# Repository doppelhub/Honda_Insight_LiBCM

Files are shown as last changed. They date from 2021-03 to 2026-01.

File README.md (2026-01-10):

# Honda_Insight_LiBCM
Replacement BCM for G1 Honda Insight Lithium Conversion
Licensed under Creative Commons - Attribution - ShareAlike 3.0
Project created and maintained by insightcentral.net user 'mudder' (a.k.a. John Sullivan).

LiBCM is a replacement computer that allows the G1 Honda Insight (2000-2006) to safely use modern lithium traction batteries.

LiBCM replaces the OEM Battery Control Module (BCM).  LiBCM is presently offered as two different 'Kits':
-'5AhG3 LiBCM Kit' uses 12S & 18S lithium battery modules from various modern Honda hybrids, or;
-'47Ah LiBCM Kit' uses 12S Samsung SDI lithium battery modules

While other lithium battery types are theoretically supported, integrating them with LiBCM is beyond the design goals for this project.  A few customers are using non-supported modules, but it requires custom BMS harnesses and also cell discharge curve characterization to create a Voc->SoC lookup table.

LiBCM officially supports the following lithium configurations:
-'5AhG3' - 48S ONLY, or;
-'47Ah'- either 48S or 60S.

NO OTHER CONFIGURATION is officially supported.  While the PCB's onboard BMS supports anywhere from 6S to 60S, you're on your own (firmware-wise) if you want to run anything besides 48S.  Future firmware updates might allow 54S and/or 60S support. 

See linsight.org for more information.

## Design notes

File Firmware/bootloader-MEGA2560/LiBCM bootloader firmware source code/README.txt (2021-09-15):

This custom MEGA2560 bootloader allows LiBCM to initially power up fast enough to not cause P1648 CEL.

A standard MEGA2560 will otherwise work with LiBCM, but will cause P1648 at the first key-on event after the IMA power switch is turned on.  After that, as long as LiBCM has not turned itself off (e.g. due to low battery), LiBCM will remain powered up, hence no P1648 error.

If you purchased an LiBCM PCB from me, then it already has the LiBCM bootloader on it.
If you're programming your own MEGA2560, then you can load the .hex file onto your MEGA using the "Arduino as SPI burn bootloader" method (do a google search).

To compile the file (e.g. if you don't want to use the pre-compiled hex file), you will need to install avr-gcc (e.g. via homebrew in MacOS), and then make the file ("make mega2560").  This is an advanced method, and if you don't know how to do it, just install the hex file instead.

The contents of this folder generate the "stk500boot_v2_mega2560.hex" file, which is then uploaded to the Arduino MEGA.

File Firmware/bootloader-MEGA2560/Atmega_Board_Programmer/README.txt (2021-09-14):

This tool is used to create an ISP that will program an Arduino Uno to program the LiBCM bootloader onto an Arduino Mega.  This custom bootloader is identical to the shipping version, except that on power-up it checks to see if the key is turned on, in which case the bootloader immediately jumps to LiBCM firmware.

See instructions here:
http://www.gammon.com.au/bootloader

Load Atmega_Board_Programmer.ino onto an Arduino Uno, then connect it to the mega as shown in the above link.  

Open debug window at 115200 and follow instructions

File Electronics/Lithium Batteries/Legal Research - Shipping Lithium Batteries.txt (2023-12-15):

Summary:
For modules up to 300 Wh, you can ship USPS ground with:
-Limited Quantity label, and
-"Lithium batteries - forbidden for transport aboard aircraft and vessel"

No additional paperwork is required (these medium-sized cells are exempted by 49CFR173.185(c):
https://www.ecfr.gov/current/title-49/subtitle-B/chapter-I/subchapter-C/part-173/subpart-E/section-173.185
"[cells under 300 Wh] are exempt from the requirements in subparts C through H of 49CFR172

Therefore, since modules over 300 Wh are NOT exempt, the must include the following additional markings:
-UN3480 (requires hazardous shipping license at UPS... but maybe not USPS?)
-Class 9 Lithium Battery label

//////////////////////////////////////////

https://pe.usps.com/text/pub52/pub52c3_003.htm#ep898369

Postal Service standards generally limit the mailing of hazardous materials to Limited Quantity surface materials or Limited Quantity air materials as defined in 332 through 336, that meet USPS quantity limitations and packaging requirements. This allowance is limited to the following:
...
Lithium batteries, dry ice, and magnetized materials, as permitted in 349.

...

332 Limited Quantity:
https://pe.usps.com/text/pub52/pub52c3_011.htm
"A limited quantity of a hazardous material is the maximum amount of a specific hazardous material exempted from DOT labeling or packaging requirements in 49 CFR. To be eligible to ship under the DOT Limited Quantity provision, a hazardous material must list an exception in column 8A of the Hazardous Materials Table in 49 CFR 172.101"

49CFR172.101 column 8A for "lithium ion batteries" states:
-must adhere to 49CFR173.185 packaging requirements
-173.27 & 175.75 non-passenger aircraft package weight limit: 35 kg

///////////////////////////////////

349 (https://pe.usps.com/text/pub52/pub52c3_027.htm#ep900056)

349.2 Mailability
... lithium batteries ... are permitted within the specified limits provided in ... 349.222, 349.23, and 349.24

///////////////////////////////////

349.222 (same link as above)
In summary: Lithium batteries with cells weighing up to 5 pounds are mailable via surface transportation.

349.4(b)
For surface transportation, parcels containing mailable Class 9 materials must be plainly and durably marked on the address side with an approved DOT Limited Quantity ground marking unless specified in 221.1 and 325.1 (see 325.4). Surface shipments bearing the Limited Quantity ground marking are not required to include the proper shipping name and identification number.

/////////////////////////////////////
/////////////////////////////////////

UPS Dangerous Goods contract
UPS Hazardous Materials Contract Service
In order to ship hazardous materials/dangerous goods with UPS, you must enter into an Agreement that ensures compliance with applicable Regulations as well as UPS carrier requirements.  In order to use this service, you must:
-Have a UPS.com user name
-Have a shipping account
-Be in compliance with all regulatory requirements and UPS's carrier variations

/////////////////////////////////////
UPS guidelines:
https://www.ups.com/assets/resources/webcontent/en_US/pack_ship_batteries.pdf

UPS does not allow UN3480 (Lithium Ion Batteries (by themselves)) without a "UPS Dangerous Goods Contract".
but does allow UN3481 (Lithium Ion Batteries contained in equipment)

"air shipments of lithium ion (UN3480) and lithium metal (UN3090) batteries without equipment must be sent as fully regulated dangerous goods when shipped with UPS, which requires a UPS Dangerous Goods contract."

"lithium ion or metal batteries may be classed as “packed with equipment” or “contained in equipment” when
the batteries accompany or are installed in apparatus for which the lithium batteries will provide electrical power for operation."

"For fully regulated shipments, the Class 9 Lithium Battery label is required."

"For ground shipments, the markings shown above are common in most countries around the world (see ADR SP 188, TDGR SP 34, or check local regulations). The U.S. additionally requires ground shipments of small lithium batteries to be identified as forbidden on passenger aircraft. The Cargo Aircraft Only label may be used, or either of the following statements, in letters at least 6 mm high:
-LITHIUM ION BATTERIES-
FORBIDDEN FOR TRANSPORT ABOARD PASSENGER AIRCRAFT"
^^^FedEx has the same requirement...
^^^...because this is a federal law: 49CFR173.185(C)(1)(iv):
"For transportation by highway or rail only, the lithium content of the cell and battery may be increased to ... 60 Wh for a lithium ion cell or 300 Wh for a lithium ion battery, provided the outer package is marked: “LITHIUM BATTERIES - FORBIDDEN FOR TRANSPORT ABOARD AIRCRAFT AND VESSEL.”"

"The U.S. also allows unique exceptions on the ground for medium lithium batteries, not recognized in other international regulations. For lithium ion, medium cells have > 20 Wh but ≤ 60 Wh; and medium batteries have > 100 Wh but ≤ 300 Wh.  Medium lithium cells/batteries may be shipped by ground as lightly regulated, provided they have the appropriate lithium ion or lithium metal mark (as shown above) and display the following marking:
LITHIUM BATTERIES—FORBIDDEN FOR TRANSPORT ABOARD AIRCRAFT AND VESSEL.”

Figure 8 - Flowchart (page 9):
Is lithium battery greater than 100 Wh? Yes
Is lithium battery less than 300 Wh OR cells less than 60 Wh? Yes
Does the package contain lithium ion batteries packed with equipment? NO
Does the package contain lithium ion batteries contained in equipment? NO
Is the gross package weight greater than 30 kg? NO
Result:
Your package does not need to be shipped as fully regulated Dangerous Goods. Please see U.S. DOT Hazardous Materials Regulations for further details about shipping requirements.
Required: Warning markings stating “Lithium Batteries – Forbidden for Transport Aboard Aircraft and Vessel,” lithium ion battery mark.

/////////////////////////////////////////////////////////////

https://www.ups.com/media/en/lithium_batteries_guidance.pdf

/////////////////////////////////////////////////////////////
Lots of packaging-specific examples:
https://www.rrc-ps.com/fileadmin/Dokumente/Shipment/Shipping_Guidelines_Lithium_Ion_Batteries_EN.pdf
5.2. Shipment of Lithium Ion Batteries > 100 Wh by Truck / Rail (ADR/RID), Sea Freight (IMDG)
A passed transportation test according section 38.3 of the UN Manual of Tests and Criteria is required!

Critical: Passing of safety tests for lithium batteries and cells (Refer to the UN Manual of Tests and Criteria
- UN/DOT 38.3). This will be indicated in the test summary document requested from your supplier.
• There are recordkeeping requirements for this testing which can be found in 49CFR173.185.

49CFR173.185:
https://www.ecfr.gov/current/title-49/subtitle-B/chapter-I/subchapter-C/part-173/subpart-E/section-173.185
"Beginning January 1, 2022 each manufacturer and subsequent distributor of lithium cells or batteries manufactured on or after January 1, 2008, must make available a test summary."

/////////////////////////////////////////////////////////////

Fedex course:
http://www.shipsafeshipsmart.com/ProductSubCats.aspx?SubCatID=5
https://www.fedex.com/content/dam/fedex/us-united-states/services/Shipping-Lithium-Batteries-via-FedEx-Ground.pdf

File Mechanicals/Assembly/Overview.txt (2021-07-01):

THIS IS A WORK IN PROGRESS

Assembly instructions:

0: Tear pack down to core.
	Keep:
	-Fan shroud (drill 0.75" hole)
	-QTY6 self-tapping screws
	-Side cover and QTY6 screws
	-QTY4 MCM bolts
	-QTY2 longest bolts
	-QTY2 high current spacers
	-QTY6 junction board bolts
	-QTY8 fan shroud bolts
	-Junction board (we'll modify below)
	-MCM'E' connector (we'll modify below)
	-Temp Sensor Harness (broken down as shown)
	-Core (with inserts) (we'll modify below)

1: Core modifications
	-Drill QTY3 0.75" holes for high current lead
	-Drill QTY6 holes for PCB
	-Add stickers

2: Batteries
	-Add stickers

2: Junction board modifications
	-Covers: 5

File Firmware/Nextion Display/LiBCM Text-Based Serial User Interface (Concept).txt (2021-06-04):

Welcome to LiBCM
version:1.21 2021APR17

'H' to Return to this Home screen
'P' to Return to Previous Screen

Enter command:
1: System Status
	Power-On Time: 1234 seconds
	Pack Configuration: 42S
		
	A: Display values since last reset
		Data Since Last Reset ('R' to reset):
		Vcell(min):	2456 mV @ C34
		Vcell(max):	3958 mV @ C34
		Vdelta:		0123 mV (C24-C32)
		Vpack:		123 Vmin, 145 Vmax
		SoC:		010% min, 078% max	
		Tpack:		10 C min, 45 C max
		Iregen(max):	078 A (actual) 
		Iassist(max):	134 A (actual)
		Total Assist:	1234 Ah (actual)
		Total Regen:	1456 Ah (actual)
		Time:		345232 s
	B: Display values since last full charge	
		Same as above, except 'Data Since Last Full Charge'
	C: Display realtime data
		U: Update Once
		C: Update Continuously ('Q' to stop)
		Vcell(min):	2456 mV @ C34
		Vcell(max):	3958 mV @ C34
		Vdelta:		0123 mV (C24-C32)
		Vpack:		123 V
		SoC:		010%	
		Tpack (min):	10 C
		Tpack (max):	12 C
		Ibatt:		078 A
		Key is: ON
		Grid Charger AC Present?: YES
		Grid Charger Powered: NO
		Grid Charger Power Output: 100%

	D: Read Raw Cell Voltages (mV)
		C: Update Continuously ('Q' to stop)
		C01-C12: 3245 3245 3245 3245 -  3245 3245 3245 3245 -  3245 3245 3245 3245
		C13-C24: 3245 3245 3245 3245 -  3245 3245 3245 3245 -  3245 3245 3245 3245
		C25-C36: 3245 3245 3245 3245 -  3245 3245 3245 3245 -  3245 3245 3245 3245
		C37-C48: 3245 3245 3245 3245 -  3245 3245 3245 3245 -  3245 3245 3245 3245
		C49-C60: 3245 3245 3245 3245 -  3245 3245 3245 3245 -  3245 3245 3245 3245
		C61-C72: 3245 3245 3245 3245 -  3245 3245 3245 3245 -  3245 3245 3245 3245
		C72-C84: 3245 3245 3245 3245 -  3245 3245 3245 3245 -  3245 3245 3245 3245
	
	E: Read Raw temperature data (degC)
		C: Update Continuously ('Q' to stop)
		GRN(Bay1): 34 C
		WHT(Inlet): 23 C
		YEL(Outlet): 35 C
		RED(Bay3): 29 C
		BMS_C01-C12: 30 C
		BMS_C13-C24: 30 C
		BMS_C25-C36: 30 C
		BMS_C37-C48: 30 C
		BMS_C49-C60: N/A
		BMS_C61-C72: N/A
		BMS_C72-C84: N/A

	F: Read Raw BATTSCI Data (from MCM)
		U: Update Once
		C: Update Continuously ('Q' to stop)

	G: Read Cell Balance Status
		Note: '1' if cell is balancing 
		C: Update Continuously ('Q' to stop)
		C01-C12: .... ..1. 1...
		C13-C24: .... .... ....
		C25-C36: .1.. .... ....
		C37-C48: .... .... ....
		C49-C60: .... 1... ....
		C61-C72: .... .... ....
		C72-C84: .... .... 1...

2: Configure Parameters
Note: These parameters cannot be change if a DIP switch on the PCB is set
	A: BMS Settings
		A: Minimum cell discharge voltage: 2750 mV
			Enter new cell Vmin ('P' to abort): 
			Example: '2750' sets Vmin to 2750 mV
			Set Vmin to 2750 mV? (Y/N)
		B: Maximum cell charge voltage: 4100 mV
			Enter new cell Vmax ('P' to abort): 
			Example: '4100' sets Vmax to 4100 mV
			Set Vmax to 4100 mV? (Y/N)
		C: Pack Ampacity: 4657 mAh
			Enter new pack size in mAh ('P' to abort):
			Example: '8000' sets pack size to 8000 mAh
			Set pack size to 8000 mAh? (Y/N)
		D: Pack SoC: 45.5%
			Enter new SoC percent as Integer ('P' to abort):
			Example: '76' sets SoC to 76%
			Note: This is the usable pack SoC, based on min/max cell voltage settings
			Set SoC to 76%? (Y/N)

	B: Temperature Settings
		A: Fans turn on at:	        23 C 
		B: Fans full speed at:	        35 C
		C: Fans disabled below:	        25% SoC
		D: Disable Grid Charging above: 45 C@pack

		N: OEM Sensor Names
			A: GRN: "Bay1"
				Enter new name for GRN temp sensor:
			B: WHT: "Inlet"
				Enter new name for WHT temp sensor:
			C: YEL: "Outlet"
				Enter new name for YEL temp sensor:
			D: RED: "Bay3"
				Enter new name for RED temp sensor:
		
	C: Grid charger settings
		E: Grid Charger installed?: Y
			Is grid charger installed? (Y/N): Y
		M: Disable Grid Charge Above SoC: 75%
			Enter new maximum grid charge SoC as Integer:
			Example: '70' disables grid charger above 70% SoC 

	D: MCM Voltage/Current Spoofing
		P: Presets
			Configure Voltage/Current Hacks (existing: B)
			A: 42S with no Current Hack
			B: 48S with no Current Hack
			C: 42S with +40% Current Hack
			D: 48S with +40% Current Hack
			
		A: Scale Current sent to MCM by: 100%
			Enter new scaled current percentage as Integer ('P' to abort):
			Note: This is the actual multiplier applied to the raw current sensor reading.
			Note: Any value besides '100%' requires external hardware modifications to MCM.
			Example: '+40% current hack' is 72% (1/1.4), because 140A*0.71=100A 

		B: Scale Voltage sent to MCM @ 0% SoC by: 100%
			Note: This value must be between 80-100%
		C: Scale Voltage sent to MCM @ 100% SoC by: 80% 
			Note: This value must be between 80-100%
			Note: Useful for high voltage packs
		Note: VPIN must be connected to LiBCM for this to work.

	F: Restore Defaults
		Restore LiBCM to default values.  This cannot be undone.
		RESET ALL STORED DATA? (y/n):

	G: Debug
		A: Configure METSCI FRAME 'A'
		B: Configure METSCI FRAME 'B'
		C: Configure METSCI FRAME 'C'
		D: Configure METSCI FRAME 'D'
		E: Toggle Fans
		F: Toggle Grid Charger
		G: Set Grid Charger PWM
		J: Restart

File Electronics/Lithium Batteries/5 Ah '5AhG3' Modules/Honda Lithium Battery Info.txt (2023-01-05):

Honda Models
STEP WGN SPADA
SPORT HYBRID i-MMD
FREED i-DCD
NSX
i-MMD

CR-Z (EH5)(2011-2014):
	IMA PN: 1D010-RBJ-C00 or 1D010-RBJ-A00

Accord Hybrid (EH5)(2014-2015):
	IMA PN: 1D070-5K1-406RM & 1D070-5K1-405RM & 5 more
	Found eBay picture with blue cells shown.

Accord Hybrid (EHW5)(2018-2020):
	IMA PN: 1D070-6C2-305
	Found eBay picture showing assembled battery at 259 V
	It's probably this car... maybe new insight.

Clarity Fuel Cell (EHW5)(2017-2020):
	IMA PN: 1D100-5WM-A01RM

NSX (EHW5)(2016)

Honda Insight (2019):
	IMA PN: 1D070-6L2-A00
	Found eBay picture showing assembled battery

Battery info:
Make: Blue Energy (Panasonic?)
Model: EHW5
Ah: 5 (charged to 4.2 volts)
Vnom: 3.6
Operating range: -30 degC to 55 degC (131 degF)
Cycle life: 50,000 (@10-85% SoC), continuous 40A charge/discharge!
Time Life: 10 years
Recommended charge/assist current: 200 A
Maximum charge/assist current: 300 A (60C)
Power density: 4.9 kW/kg
Used in Honda's i-MMD hybrid cars

Label that comes with batteries contains: "UF121285H"
Searching online finds just one result (blue energy EHW5 battery):
https://zhuanlan.zhihu.com/p/349899001
Key findings here: 
	Says from Honda immd hybrid
	Chemistry: LiNiCoMnO2 (ternary lithium battery)(NMC)
	"Panasonic used after localization, model UF121285H"
	"At present, the detailed specifications of this battery of Panasonic are not available online, but because Honda directly replaces it, we have reason to believe that the specifications of the two batteries are compatible.
	"UF 12 12 85" is based on cell dimensions (120 x12 x 85 mm)

Blue Energy is 49% owned by Honda (and 51% by GS Yuasa Int Ltd)
https://www.blue-energy.co.jp/en/

...

Post to ic.net:
From Honda immd hybrid system, which is used in both 2018-2020 Accord Hybrid & 2019+ Insight
Chemistry: LiNiCoMnO2 (ternary lithium battery)
"Panasonic used after localization, model UF121285H". I think he means that the battery was originally designed by Blue Energy (which itself is 49% owned by Honda)... and now Panasonic is making the pack instead. Remember: the box that these modules shipped in has Panasonic written all over it, as do the various labels.
"At present, the detailed specifications of this battery of Panasonic are not available online, but because Honda directly replaces it, we have reason to believe that the specifications of the two batteries (Panasonic vs Blue Energy) are compatible."
"UF 12 12 85" is based on cell dimensions (120 x12 x 85 mm).

Cell information:
Model: EHW5
Ah: 5 (when charged to 4.2 volts)
Vnom: 3.6
Operating range: -30 degC to 55 degC (131 degF)
Cycle life: 50,000 (@10-85% SoC), continuous 40A charge/discharge!
Time Life: 10 years
Recommended charge/assist current: 200 A
Maximum charge/assist current: 300 A (60C)
Power density: 4.9 kW/kg

The reason the part number on the box doesn't pull up on Honda's website is that the pack itself is a non-user-purchasable subcomponent of the following parts:
1D070-6C2-305 (2018-2020) Accord Hybrid). OEM cost: $2762 
1D070-6L2-A00 (2019 Insight Hybrid). OEM cost: $3126

So yeah, this $440 battery is ~$2800 from Honda.

...

'5AhG3' cell: 70c 5.5ah Panasonic cells UF121285h

There is also a UF121285 which seems to be the CMAX, VW, and Honda fit cell with a rating 150A vs 375A for the h version

...

18S Module weight:
-total: ~14 pounds
-cells: ~10 pounds
-everything else: ~4 pounds

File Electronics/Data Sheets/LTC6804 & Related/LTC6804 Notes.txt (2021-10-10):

ltc6804 notes

When REFUP==1, 12-cell ADC measurement+cal tcycle= 2480 microseconds max (normal mode)
When REFUP==1,  2-cell ADC measurement+cal tcycle= 430 microseconds max (normal mode)
Doesn't make sense to switch to 2-cells per loop, as the voltages no longer sampled simultaneously. 

open wire detection:

current/power consumption.  Note wasteful LDO has up to 45 volt drop (@4.17 volts/cell), hence it consumes much more power than LTC itself.
Number format: {maxCurrent_uA}(P_LTC_mW)[P_LDO_mW]

Core pulls:
When sleeping:               {6 uA}(  0.0 mW)[  0.3 mW]
When standby & REFUP == 0: {650 uA}(  3.3 mW)[ 29.3 mW]
When REFUP active:         {750 uA}(  3.8 mW)[ 33.8 mW]
When actively measuring: {12300 uA}( 61.5 mW)[553.5 mW]

isoSPI adds additional current:
ready:  {5800 uA}(29.0 mW)[261.0 mW]
active: {7300 uA}(36.5 mW)[328.5 mW]

Therefore, worst case power is: {19600 uA}( 98.0 mW)[882.0 mW]
Since measurement duty is ~50%, the average LDO power is ~600 mW.

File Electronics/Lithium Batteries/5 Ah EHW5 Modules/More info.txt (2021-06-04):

Cell Specifications:

NMC cell chemistry
Low 2.8V high 4.2v
Nominal 3.6v
120.7 mm L
13.3 mm W
100 mm H with terminals.
Terminal size: M5 0.8
1lb 8oz
Capacity:  5 Ah
Capacity: 18.75 Wh
60C

Cell voltages:

4.2V = 100% SOC (Absolute MAX)
4.1V = 90% SOC (recommended max)
3.7V = 70% SOC
3.5V = 20% SOC (recommended min)
3V = 0% SOC

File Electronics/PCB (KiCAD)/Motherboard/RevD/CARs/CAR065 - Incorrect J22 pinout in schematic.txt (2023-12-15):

J22 text in schematic pdf is incorrect:

RevD (Incorrect):
VCC
SCK
MOSI
MISO
GPIO0
CS_EXT
GND
GND

Correct:
VCC
MOSI
SCK
MISO
GPIO0
CS_EXT
GND
GND

To fix:
Swap "MOSI" and "SCK" text.  The electrical connections should not change.
The silkscreen doesn't change... just the text for J22 in the schematic.
The silkscreen on both RevC and RevD is correct.

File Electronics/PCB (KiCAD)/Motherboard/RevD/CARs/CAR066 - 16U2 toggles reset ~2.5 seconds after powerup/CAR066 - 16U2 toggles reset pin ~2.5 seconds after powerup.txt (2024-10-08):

16U2 toggle PD7 ~2.5 seconds after powerup.  This causes pulse on MEGA2560's reset pin, which briefly disables Mega's output pins... but for some reason doesn't actually reset program execution.

This only occurs when USB cable is connected during powerup.  Given that a USB cable typically powers the 5V rail, this won't actually ever occur; in my testing that lead to this CAR, my USB cable's 5V wire was cut.

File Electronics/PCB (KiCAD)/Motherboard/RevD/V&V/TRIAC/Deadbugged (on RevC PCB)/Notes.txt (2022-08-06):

These screenshots are measured with differential probe connected across TRIAC's A1 & A2 terminals.  TRIAC is enabled (i.e. grid charger is charging).
Grid charger is HLG-480H-C2100B (2.1 amps output @ 190 Vout, using 3.5 amps input @ 123.5 Vin).

If this wave were sinusoidal, it would mean the TRIAC is sinking ~3.1 watts (3.5 A * 1.25 Vp / sqrt(2)).  However, the waveform isn't sinusoidal, so we need to use a true Vrms measurement:

Vrms with trueRMS Fluke 100: 1.228 volts
Vrms on scope: 1.20 volts.

So the actual input power is 3.5 amps * 1.228 volts = 4.3 watts

...

R_TRIAC(on) decreases as TRIAC heats up:
@Tcase = 206 degF ( 97 degC), R_TRIAC(on) = 1.022 Vrms, (RevD grid blocking diode is 200 degF).
@Tcase = 225 degF (107 degC), R_TRIAC(on) = 1.015 Vrms, (RevD grid blocking diode is 206 degF).
Tambient = 68 degF

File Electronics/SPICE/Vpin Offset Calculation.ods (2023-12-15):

 |  | multiply | 0.25
 |  | offset | 3
ADC counts | Pack voltage (actual) |  | Calculated Voltage | Error (volts)
0 | 0.0 |  | 3.0 | -3.0
50 | 12.7 |  | 15.5 | -2.8
100 | 25.4 |  | 28.0 | -2.6
150 | 38.1 |  | 40.5 | -2.4
200 | 50.8 |  | 53.0 | -2.2
250 | 63.5 |  | 65.5 | -2.0
300 | 76.2 |  | 78.0 | -1.8
350 | 88.9 |  | 90.5 | -1.6
400 | 101.6 |  | 103.0 | -1.4
450 | 114.3 |  | 115.5 | -1.2
500 | 127.0 |  | 128.0 | -1.0
550 | 139.6 |  | 140.5 | -0.9
600 | 152.3 |  | 153.0 | -0.7
650 | 165.0 |  | 165.5 | -0.5
700 | 177.7 |  | 178.0 | -0.3
750 | 190.4 |  | 190.5 | -0.1
800 | 203.1 |  | 203.0 | 0.1
850 | 215.8 |  | 215.5 | 0.3
900 | 228.5 |  | 228.0 | 0.5
950 | 241.2 |  | 240.5 | 0.7
1000 | 253.9 |  | 253.0 | 0.9
1023 | 259.7 |  | 258.8 | 1.0

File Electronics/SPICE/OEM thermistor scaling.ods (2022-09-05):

LiBCM OEM sensor w/ batt sensor math | Calibrated Thermometer | LiBCM Batt sensors | Correction | Correction
DegC | DegC |  | scaler mx+b | 8b math | math error | actual error
62 | 71 |  | 72.29 | 72.5 | 0.21 | 1.5
59 | 69 |  | 68.62 | 68.75 | 0.13 | -0.25
55 | 64 |  | 63.72 | 63.75 | 0.03 | -0.25
53 | 62 |  | 61.27 | 61.25 | -0.02 | -0.75
52 | 60 |  | 60.05 | 60 | -0.05 | 0
50 | 58 |  | 57.60 | 57.5 | -0.10 | -0.5
49 | 56 |  | 56.38 | 56.25 | -0.13 | 0.25
47 | 54 |  | 53.93 | 53.75 | -0.18 | -0.25
45 | 52 |  | 51.48 | 51.25 | -0.23 | -0.75
43 | 49 |  | 49.03 | 48.75 | -0.28 | -0.25
42 | 48 |  | 47.81 | 47.5 | -0.31 | -0.5
41 | 46 | 44 | 46.58 | 46.25 | -0.33 | 0.25
39 | 44 | 42 | 44.13 | 43.75 | -0.38 | -0.25
37 | 42 |  | 41.69 | 41.25 | -0.44 | -0.75
36 | 40 | 37 | 40.46 | 40 | -0.46 | 0
34 | 38 | 36 | 38.01 | 37.5 | -0.51 | -0.5
32 | 36 | 34 | 35.56 | 35 | -0.56 | -1
31 | 34 | 32 | 34.34 | 33.75 | -0.59 | -0.25
29 | 32 | 30 | 31.89 | 31.25 | -0.64 | -0.75
27 | 30 | 28 | 29.44 | 28.75 | -0.69 | -1.25
 | 28 |  | -3.61 | -5 | -1.39 | -33
 | 26 |  | -3.61 | -5 | -1.39 | -31
 | 24 |  | -3.61 | -5 | -1.39 | -29
20 | 21 |  | 20.87 | 20 | -0.87 | -1
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

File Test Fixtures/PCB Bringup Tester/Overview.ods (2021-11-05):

 | Low Voltage Bringup Test
Done? | Test | Onboard Mega | Pass Criteria | External Connection
Yes | 4x20 display | Send screen data to user | User can read screen | 4x20 display
Yes | Cover switch | Wait for user to push button | Test starts (user hears buzzer) | None
Yes | Buzzer | PWM buzzer at startup | User hears buzzer | None
Yes | LED1/2/3/4 | flash each LED until next step | User sees LEDs | None
Yes | HMI_EN FET working? | flash LED plugged into 1x4 connector | User sees LED | LED connected to HMI 1x4
Yes | Temp: Batteries & OEM | Turn TEMP_EN off; verify all sensors ~5V Turn TEMP_EN on; verify all sensors ~2.5V | Voltages in range | QTY7 temperature sensors
Yes | BATTSCI/METSCI | Send BATTSCI packet to external Wait for response from external | message received when expected no response when drivers off | OEM BCM connector
Yes | OEM Fan Diodes Present | nothing | Lambda Gen current = 0 When test isn't running If diodes flipped, lambda gen will drive at current limit | 12V_ALWAYS connected to onboard 12V
Yes | Onboard Fans & KeyON? | Turn FAN_PWM off; verify KeyON==yes Turn FAN_PWM on; verify KeyON==no |  | FAN- permanently connected to 12V_KEYON, with dummy load and LED
Yes | MCM_E_CONTROL | PWM various values | ADC result within limits | External LED (should blink)
Yes | VPIN_IN & VPIN_OUT | Loopback out to in | Characters match | Short VPIN_OUT to VPIN_IN
 | Current Sensor & OEM Fan H/L |  | ADC result within limits | Connect lambda gen thru OEM sensor
Yes | TURN_OFF_5V | toggles pin on/off Also verifies keyON (FAN_PWM) turns back on | screen dims | 4x20 display dims when onboard buck off
 | High Voltage Bringup Test
Yes | Flipping HVDC turns LiBCM on (HVDCDC & enable) | nothing | LiBCM turns on
 | Shorts/opens on LTC6804 | 3 cells at a time
Yes | Grid IGBT & Grid sense | standard LiBCM firmware | Grid Charger turns on

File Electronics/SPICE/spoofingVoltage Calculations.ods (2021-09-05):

Example | pack voltage (volts) | pack current (amps) | Expected Vspoof (V) | CPU Result Vspoof (V)* | op1: | Exact Equation**
A | 190 | 140 | 121 | 125 | 32030 | 121
A | 190 | 0 | 159 | 155 | 39730 | 159
A | 190 | -75 | 179 | 171 | 43855 | 179
B | 144 | 140 | 120 | 120 | 30788 | 120
B | 144 | 0 | 128 | 125 | 32048 | 128
B | 144 | -75 | 132 | 128 | 32723 | 132
**Exact equation
spoofedVoltage_mV = vPackActual_mV * ( 2 / 3 - actualCurrent_A / 215 ) + 614 * actualCurrent_A + 32,000
*CPU optimized Equation:
spoofedVoltage_V = ((vPackActual_V * (167 - actualCurrent_A) + 154 * actualCurrent_A + 8,000) >> 8
op1: (vPackActual_V * (167 – actualCurrent_A) + 154 * actualCurrent_A + 8000)
op1(magic numbers) (vPackActual_V * (AA – actualCurrent_A) + BB * actualCurrent_A + CC
vSpoof: op1 >>8
 | optimized | calculated
AA: | 167 | 167
BB: | 135 | 154
CC: | 8000 | 8000
Result: The equation should be:
spoofedVoltage_V = ((vPackActual_V * (167 - actualCurrent_A) + 135 * actualCurrent_A + 8,000) >> 8

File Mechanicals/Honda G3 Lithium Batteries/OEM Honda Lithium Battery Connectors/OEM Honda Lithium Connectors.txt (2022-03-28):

Shoutout to "Bull Dog" for finding the connector part number!  That wasn't easy.

Haidie (yqwakan.com)

12S ("HD202")(M6098-4589):
https://www.yqwakan.com/product_8258_AutoWiringHarnessElectricHousingConnector60984589.html

https://www.aliexpress.com/item/4000906238501.html?spm=a2g0o.store_pc_allProduct.8148356.14.17012fc9j7dxgb

18S ("HD281"):
https://www.yqwakan.com/product_7737_autowiringharnessplugcableelectricunsealedplugconnectorHD281072211.html

https://www.aliexpress.com/item/4000265656537.html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,searchweb201602_,searchweb201603_

...

http://www.hdconnectorstore.com/productdetail/3156.html

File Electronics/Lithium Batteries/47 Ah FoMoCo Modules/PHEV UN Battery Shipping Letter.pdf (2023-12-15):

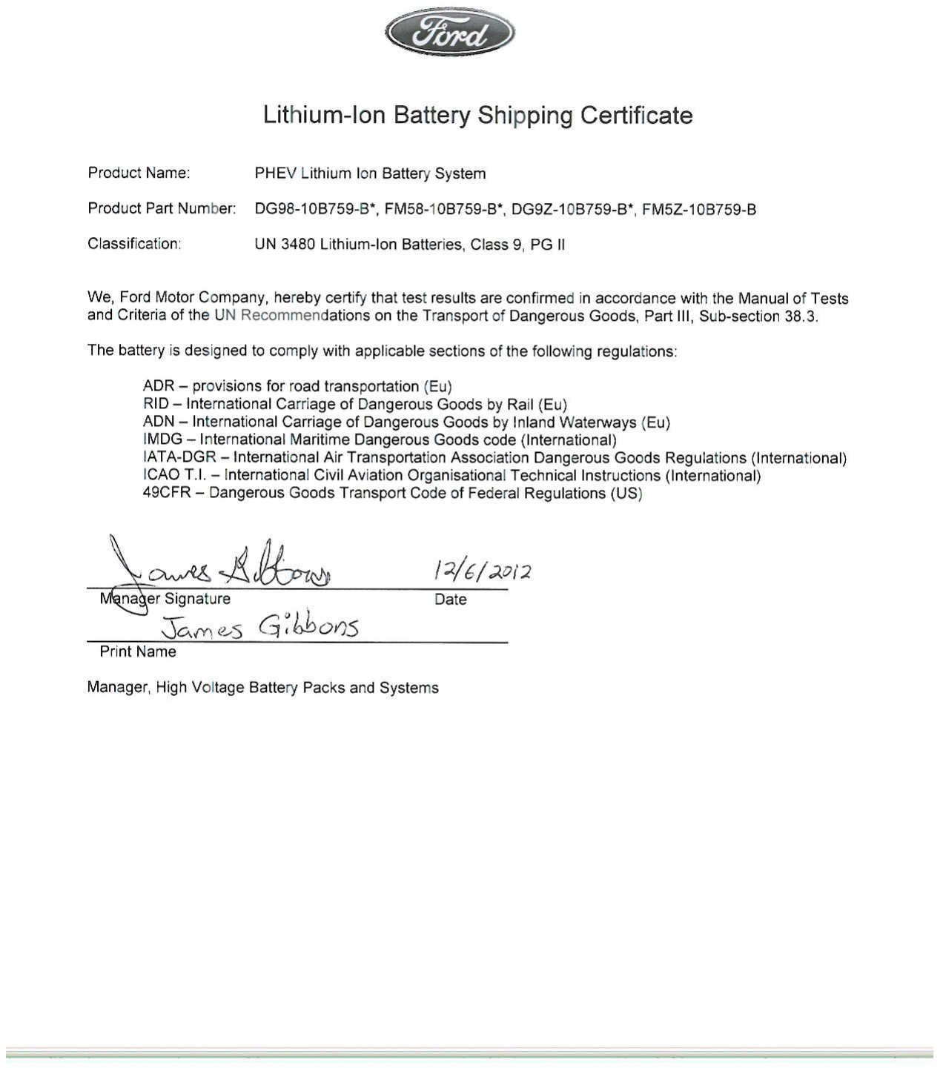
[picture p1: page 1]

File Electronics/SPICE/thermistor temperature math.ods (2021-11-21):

constants |  |  | <<Hidden columns
TEMP_BALANCE_RESISTANCE_OHMS | 10000
ADC_COUNTS_AT_VCC | 1023
TERMISTOR_BETA | 3982
THERMISTOR_RESISTANCE_23DEGC | 10000
TEMP_23DEGC_KELVIN | 296
 | countsADC | integer degC
 | 10
 | 20
 | 30
 | 40
 | 50
 | 60
 | 70
 | 80
 | 90
 | 100
 | 110
 | 121 | 75
 | 124 | 74
 | 128 | 73
 | 132 | 72
 | 136 | 71
 | 140 | 70
 | 144 | 69
 | 148 | 68
 | 152 | 67
 | 157 | 66
 | 162 | 65
 | 167 | 64
 | 172 | 63
 | 177 | 62
 | 182 | 61
 | 188 | 60
 | 193 | 59
 | 199 | 58
 | 205 | 57
 | 211 | 56
 | 217 | 55
 | 223 | 54
 | 230 | 53
 | 237 | 52
 | 244 | 51
 | 251 | 50
 | 258 | 49
 | 265 | 48
 | 273 | 47
 | 281 | 46
 | 290 | 45
 | 298 | 44
 | 305 | 43
 | 315 | 42
 | 324 | 41
 | 333 | 40
 | 342 | 39
 | 351 | 38
 | 361 | 37
 | 371 | 36
 | 380 | 35
 | 391 | 34
 | 401 | 33
 | 411 | 32
 | 422 | 31
 | 433 | 30
 | 444 | 29
 | 455 | 28
 | 466 | 27
 | 477 | 26
 | 488 | 25
 | 500 | 24
 | 512 | 23
 | 523 | 22
 | 535 | 21
 | 547 | 20
 | 559 | 19
 | 570 | 18
 | 582 | 17
 | 594 | 16
 | 606 | 15
 | 618 | 14
 | 630 | 13
 | 641 | 12
 | 653 | 11
 | 665 | 10
 | 676 | 9
 | 688 | 8
 | 699 | 7
 | 710 | 6
 | 721 | 5
 | 732 | 4
 | 743 | 3
 | 753 | 2
 | 764 | 1
 | 774 | 0
 | 784 | -1
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

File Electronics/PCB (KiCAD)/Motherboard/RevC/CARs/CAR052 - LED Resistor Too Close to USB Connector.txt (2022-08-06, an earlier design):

Resistor R5 needs to move left, for additional clearance from Arduino MEGA USB connector.

Workaround: Manually verify no short, then apply conformal coating.

/////////////////////////////////////////////////////////////////////////////////

Solution:
Moved R5 below D4

Done

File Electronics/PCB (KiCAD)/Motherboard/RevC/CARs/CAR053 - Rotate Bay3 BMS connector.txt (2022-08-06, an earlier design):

Rotate J13 180 degrees, so right angle latching connector can be used.

/////////////////////////////////////////////////////////////////////////////////

Solution:
No change.  Existing design works.

Done

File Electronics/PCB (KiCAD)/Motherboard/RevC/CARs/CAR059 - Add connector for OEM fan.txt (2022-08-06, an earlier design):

Add OEM fan connector (possibly use existing screw terminals)?

/////////////////////////////////////////////////////////////////////////////////

Solution:
Did not add OEM fan connector

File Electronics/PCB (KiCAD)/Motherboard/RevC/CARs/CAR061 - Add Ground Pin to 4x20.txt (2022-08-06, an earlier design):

Add a 5th (unpopulated?) ground pin hole for 4x20 cable

/////////////////////////////////////////////////////////////////////////////////

Solution:
Did not add; 4x20 is prototype only

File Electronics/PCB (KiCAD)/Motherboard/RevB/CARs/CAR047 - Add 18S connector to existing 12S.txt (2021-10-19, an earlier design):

Make it easier to plug in 54S pack.
Consider replacing last LTC6804 with a 6 cell version?

/////////////////////////////////////////////////////////////////////////////////

Solution:
Did not add 18S footprint

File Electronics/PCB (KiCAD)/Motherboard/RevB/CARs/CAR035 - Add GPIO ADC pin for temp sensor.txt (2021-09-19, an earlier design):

Add temp sensors that are attached directly to each battery.

Bolt-on sensor that plugs into headers on LiBCM PCB
900-2138651635-ND
We'll need to oversize the mounting hole.  Also, orange covers won't fit... but whatever.

The temperature sensor includes Molex connector WM17043-ND, which is rectangular with widest exterior dimensions: 4.12x4.5 mm
We'll need to add three holes in PCB, so the wire can slide thru (and mount to the surface mount connector)

Mating Molex connector (surface mount only):
WM26831CT-ND

Also add standard 0.1" thru hole connector (e.g. underneath this connector... is case any of them proprietary parts become unobtanium.

Finally, need to add an extra HVDC isolation around wire... it needs to be able to fit around either the ring terminal (dimensions unspecified) or the Molex connector (4.12x4.5 mm)... or else we'll need to remove the terminals from their housings, and then reinsert them (fun fun).

Trying this extra shielding out: P1056CL005-ND

/////////////////////////////////////////////////////////////////////////////////

Solution:
Temp sensor: 900-2138651635-ND
Need to add wire holes thru PCB
Add SMT connector: WM26831CT-ND

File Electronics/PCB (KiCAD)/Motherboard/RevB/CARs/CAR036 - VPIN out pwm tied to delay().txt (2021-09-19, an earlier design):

VPIN_OUT PWM is tied to Arduino's internal timer, which controls delay(), etc.  Default runs at ~1 kHz, which is a bit slow for VPINout.

Consider changing VPIN_IN LPF to 10k + 100n
Don't increase tau on VPIN_OUT, because it's already 10 ms... MCM throws an error if it takes too long.

Consider swapping mega P12 with mega P4, so VPIN_OUT can use MEGA P12 PWM.

/////////////////////////////////////////////////////////////////////////////////

Solution:
VPIN_OUT_PWM now connects to MEGA P12
VPIN_IN_NOISY LPF is (768 Ohms + 1 uF)

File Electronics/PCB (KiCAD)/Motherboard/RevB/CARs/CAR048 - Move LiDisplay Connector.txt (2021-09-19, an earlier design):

Move LiDisplay connector to top of PCB (so it can be plugged in after-the-fact.
2057-CDR-04-GR-ND

/////////////////////////////////////////////////////////////////////////////////

Solution:
2057-CDR-04-GR-ND

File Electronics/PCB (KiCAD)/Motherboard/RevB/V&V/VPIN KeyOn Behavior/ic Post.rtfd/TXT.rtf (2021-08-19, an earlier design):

Today I finally got around to measuring the VPIN startup behavior. It turns out LiBCM has quite a bit more time than I thought it would to boot up and get ready to spoof VPIN: as shown below, it takes ~200 ms for the MCM to startup and process VPIN.

In this first picture, LiBCM is installed, but VPIN isn't connected to it. VPIN is passing through an inline 5.6kOhm resistor, but is otherwise OEM:
YEL: VPIN@PDU
GRN: VPIN@MCM
PNK: (12V+10s)
BLU: HVDC@PDU
¬

In this picture we're looking at the MCM's powerup timing diagram, and can deduce the following:
-t=0 is when PNK (12V+10s) rapidly rises (because we just turned the key on).
-from t=0 to 200ms, VPIN is loosely floating (because I/O is uninitialized)
-@191 ms HVDC@PDU starts charging (through pre-charge circuit)
-@203 ms VPIN starts tracking HVDC (because MCM has finished starting up and toggled I/O correctly to track VPIN)
-@331 ms MCM fires main contactor (HVDC@PDU is still 18 volts below HVDC@pack).
-@346 ms contactor mechanically engages, so HVDC@PDU rapidly rises to HVDC@pack.

Thoughts:
-I don't think the MCM cares about the VPIN charge curve... it's simply looking for VPIN*52 ~= (V_MCM'E' - ~20 volts) before a timeout occurs.
-Thus, LiBCM shouldn't need to frantically update VPIN when the key first turns on... instead, we can just update the VPIN voltage as part of the superloop.

Let's look at LiBCM's behavior as it stands today (RevB HW running 0.0.15 FW). There are two unique cases:
1) If LiBCM is already running when the key turns on**, then LiBCM won't even break a sweat spoofing VPIN. Piece of cake:
¬
If the Arduino is already initialized, then keyON (PNK) to toggling LED2 (GRN) takes 16.8 ms, which leaves us 183.2 ms to do whatever we want prior to needing to sample VPIN_IN and update VPIN_OUT.

2) However, if LiBCM is unpowered when the key turns on**, the MCM will presently throw a P-code, as it simply takes too long to get everything up and running.

**Fortunately, under normal operating conditions LiBCM always remains on. Specifically, LiBCM will only be off under the following two conditions:
-If this is the first keyON event to occur after turning on the IMA switch, or;
-If LiBCM previously turned itself off, which only occurs if the HV battery gets critically low (to prevent over-discharging the pack).

Starting with the power supply, we can see that the 5 volt rail ramps up quite fast: less than 3% of our timing budget (6 ms / 200 ms):
¬

Next we see that the default MEGA2560 fuse settings configure the microcontroller to hold itself in reset for ~66 ms, to give the16 MHz oscillator time to start. Right now this delay eats up 33% of our timing budget (we've now consumed 36% in total). We can reduce this delay - possibly down to 4 ms - by reprogramming the fuses, but we'd need to characterize the oscillator's startup behavior. This is a moot issue for now, due to the next step in the process.

Things go downhill from there... after coming out of reset, the Arduino jumps to an in-memory bootloader, which waits for ~700 ms for the (possibly connected) host computer to (potentially) start downloading a new program. This delay alone is 3.5 times our entire budget (200 ms). We could remove this bootloader, but then LiBCM wouldn't be firmware-upgradable via USB; you'd need an external programmer (yuck).

If we add this all up, right now it takes 908 ms from powerup to toggling LED1 (YEL signal):
¬
This step exceeds our entire timing budget just over 4.5x.

One solution to this problem is to modify the bootloader to check whether the "OPTION" mechanical switch (on the LiBCM PCB) is turned on or off:
-If the switch is on, the bootloader immediately exits (without waiting); programming via USB is not allowed, but LiBCM will meet 'cold start' timing requirements.
-If the switch is off, the bootloader waits ~700 ms (as described above); programming via USB is allowed, but LiBCM will only respond to a keyON event fast enough if it's already on before the key turns on**.

Presumably tinkering types would leave the switch off, knowing that they'd need to manually turn on LiBCM each time after turning on the IMA switch (e.g. by plugging the USB cable into a portably lithium USB pack). Another option would be to just accept the first-time-on P-code, then turn the car back off and back on, and then clear the P-code (via OBDIIC&C or unplugging 12 volt battery).

And those that don't care about firmware upgrades could leave the switch on (default position), knowing that the firmware isn't upgradable (unless they turn the switch off.

Awesome, so now we've conceptually solved the "keyOn to toggling LED1" problem, so we're all good, right?
Ha, no!
In the above plot, we immediately toggled LED1, prior to initializing anything else (e.g. USB, METSCI, BATTSCI, the LTC6804s, etc).
If we toggle LED2 (GRN) after initializing everything, we see that the existing (terrible) architecture adds an additional 1240 ms, which blows our timing budget by an additional 6x:
¬
We can certainly reduce this time considerably by (eventually) removing the Arduino-specific initialization functions, which are glacially slow.
We could also have a special startup handler that only loads the absolute bare essentials required to spoof VPIN on first powerup, and then later load everything else.

Putting it all together, right now the Arduino takes more than ten times longer to "turn on" than the timing budget allows.
This will result in a P-code error if LiBCM is powered down** when the key is turned on.

In summary: We're going with option 1 for now; LiBCM will need to be manually powered on the first time after the IMA switch is turned on (or else you'll receive a P-code). After that, LiBCM will remain on, so no P-codes will occur on subsequent keyON events.

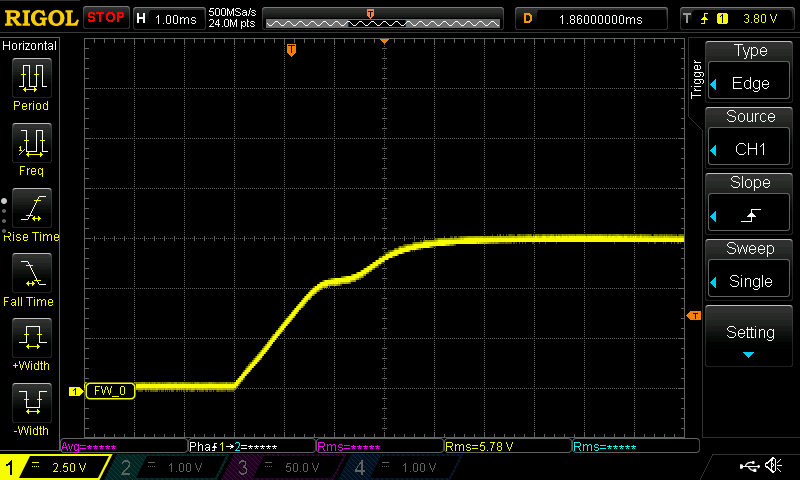
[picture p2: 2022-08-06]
Electronics/PCB (KiCAD)/Motherboard/RevD/V&V/TRIAC/Deadbugged (on RevC PCB)/60S TO220 SIHP068N60EF (FET) 5 Arms - Vgs during turnon.png

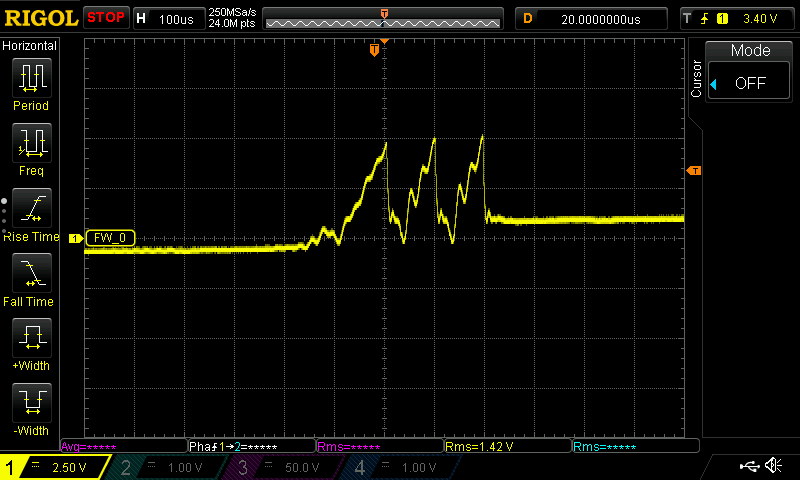
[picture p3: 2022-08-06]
Electronics/PCB (KiCAD)/Motherboard/RevD/V&V/TRIAC/Deadbugged (on RevC PCB)/LiBCM RevD TRIAC voltage drop - 3.png

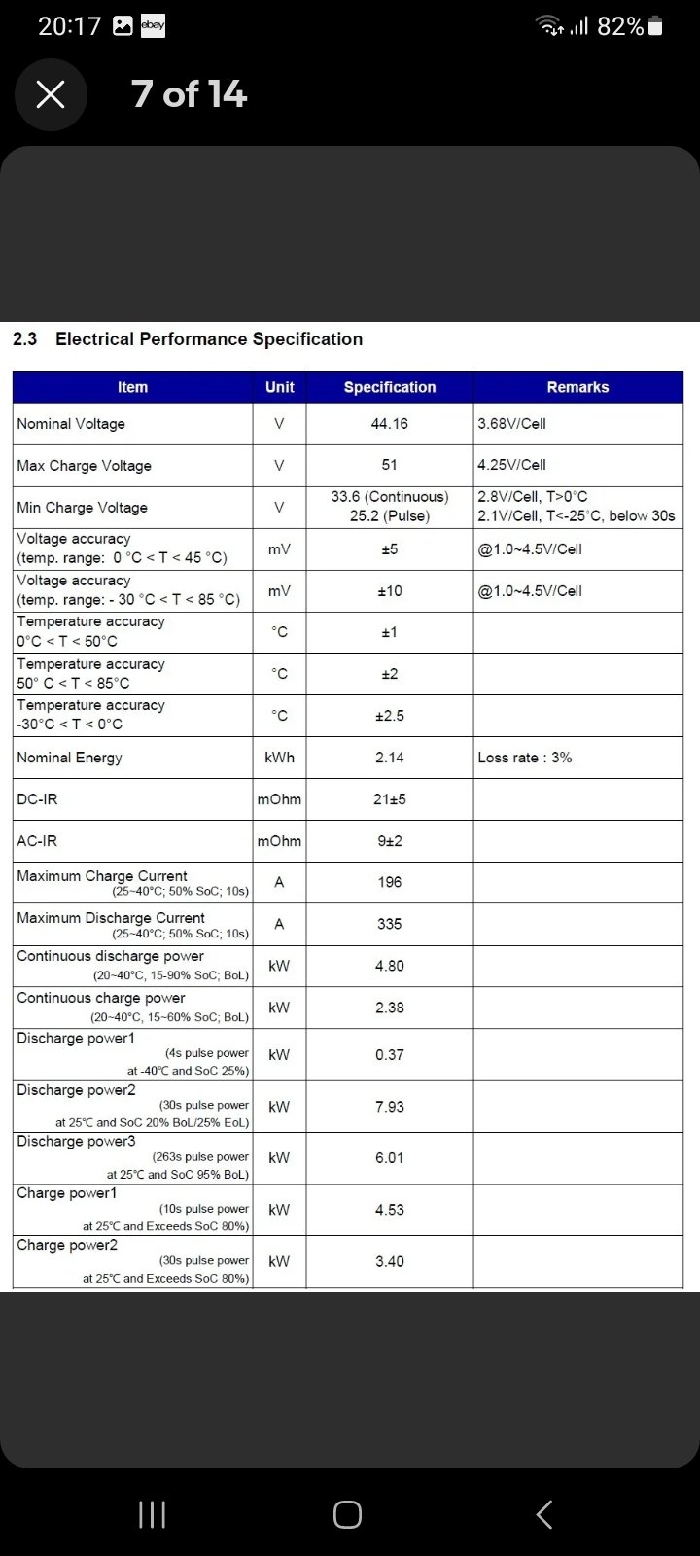
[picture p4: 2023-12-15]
Electronics/Lithium Batteries/47 Ah FoMoCo Modules/Spec/Page2.jpg

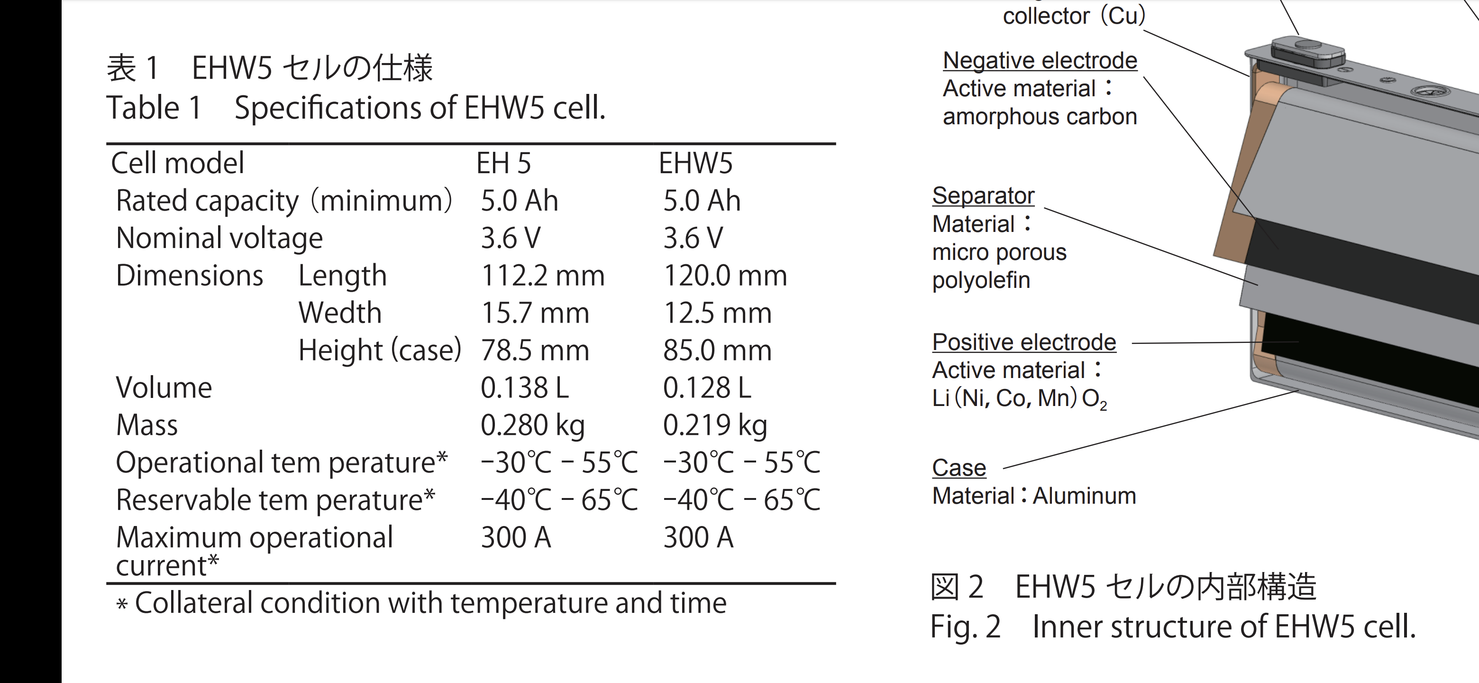
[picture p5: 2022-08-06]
Electronics/Lithium Batteries/5 Ah EHW5 Modules/Cell Structure.png

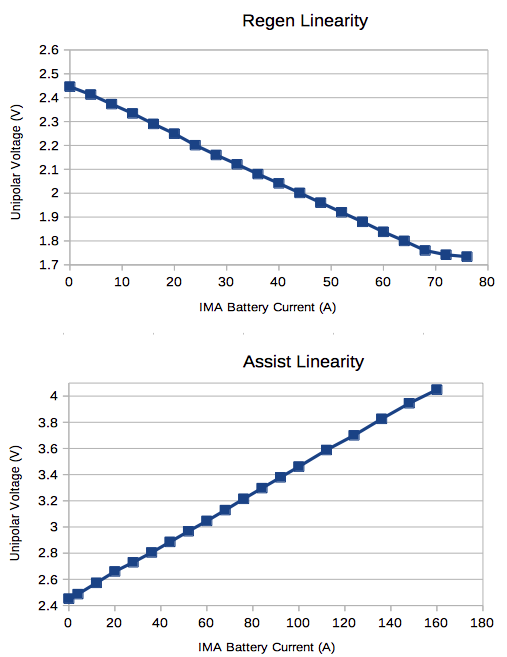
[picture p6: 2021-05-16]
Electronics/Data Gathered from OEM/BCM Linearity.png

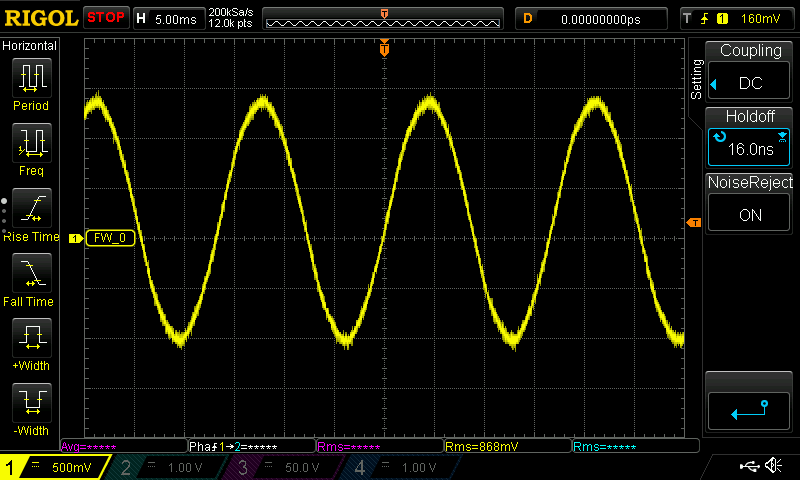
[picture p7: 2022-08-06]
Electronics/PCB (KiCAD)/Motherboard/RevD/V&V/TRIAC/Deadbugged (on RevC PCB)/60S TO220 SIHP068N60EF (FET) 5 Arms HS'A' - 85 degC @ Tambient.png

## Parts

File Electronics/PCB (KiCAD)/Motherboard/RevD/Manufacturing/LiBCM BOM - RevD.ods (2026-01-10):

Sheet: LiBCM BOM
 |  |  | 0 | QTY47Ah
 |  |  | 65 | QTY05Ah
Part Description | Supplier | Part Number | QTY /5Ah | QTY/ 47Ah | $/ Part | $/ 5Ah LiBCM | $/ 47Ah LiBCM | $/ QTY n LiBCMs (n=above) | QTY needed For n LiBCMs | 2024DEC QTY on Hand | 2024DEC Inventory Value ($) | 2025APR QTY on Hand | grams /unit | Additional QTY to order for 'n’ PCBs | QTY Ordered | Last Purchase Supplier
Pick & Place
Raw PCB | Seeedstudio | RevD | 1 | 1 | $8.59 | $8.59 | $8.59 | $558.49 | 65 | 21 | $180.44 | 130 | - | 0 | 100
Resistor – 20 | Digikey | RMCF0805JT20R0 | 17 | 17 | $0.00 | $0.06 | $0.06 | $3.76 | 1105 | 5450 | $18.53 | 4000 | - |  | 0
Resistor – 75 | Digikey | ERJ-12ZYJ750U (existing) RMCF2010FT75R0 (have a reel) RMCF2010JT75R0 (cheaper) | 61 | 61 | $0.04 | $2.32 | $2.32 | $150.67 | 3965 | 1600 | $60.80 | 5900 | - | 0 | 10000 | oc
Resistor – 100 | Digikey | RMCF0805FT100R | 100 | 100 | $0.00 | $0.40 | $0.40 | $26.00 | 6500 | 5450 | $21.80 | 6700 | - | 0 | 10000 | DigiKey
Resistor – 768 | Digikey | RMCF0805FT768R | 10 | 10 | $0.00 | $0.04 | $0.04 | $2.60 | 650 | 9390 | $37.56 | 7800 | - |  | 0
Resistor – 1k24 | Digikey | RMCF0805FT1K24 | 86 | 86 | $0.00 | $0.34 | $0.34 | $22.36 | 5590 | 9400 | $37.60 | 8200 | - |  | 5000 | DigiKey
Resistor – 7k32 | Digikey | RC0805FR-077K32L | 14 | 14 | $0.01 | $0.08 | $0.08 | $4.95 | 910 | 5650 | $30.74 | 3700 | - |  | 0
Resistor – 10k @ 250 mW | Digikey | AC0805FR-7W10KL | 29 | 29 | $0.01 | $0.32 | $0.32 | $20.74 | 1885 | 2200 | $24.20 | 4820 | - |  | 4792 | Newark
Resistor – 71k5 | Digikey | RMCF0805FT71K5 | 7 | 7 | $0.00 | $0.02 | $0.02 | $1.59 | 455 | 3200 | $11.20 | 2450 | - |  | 0
Resistor – 100k @ 250 mW | Digikey | RK73H2ATTD1003F | 8 | 8 | $0.01 | $0.04 | $0.04 | $2.60 | 520 | 2800 | $14.00 | 1800 | - |  | 0
Resistor – 5M1 | Digikey | RMCF1206JT5M10 | 11 | 11 | $0.00 | $0.04 | $0.04 | $2.65 | 715 | 2100 | $7.79 | 1390 | - |  | 0
Capacitor – 100p | Digikey | CL21C101JC61PNC | 12 | 12 | $0.02 | $0.26 | $0.26 | $17.16 | 780 | 1200 | $26.40 | 2300 | - |  | 2000 | Newark
Capacitor – 22n | Digikey | CGA5K4X7R2J223K130AA | 14 | 14 | $0.08 | $1.11 | $1.11 | $72.07 | 910 | 2200 | $174.24 | 1080 | - |  | 0
Capacitor – 68n | Digikey | C1206C683KCRACAUTO | 2 | 2 | $0.14 | $0.27 | $0.27 | $17.63 | 130 | 425 | $57.65 | 275 | - |  | 0
Capacitor – 100n | Digikey | CL21B104KCC5PNC (existing) CL21B104KCFWPJE (existing) CL21B104KCFSFNE (soft term) | 89 | 89 | $0.03 | $2.85 | $2.85 | $185.12 | 5785 | 3500 | $112.00 | 6700 | - | 0 | 10000 | Arrow
Capacitor – 1u | Digikey | CL21B105KAFNNNE (existing) 08053C105K4Z2A (soft term) | 40 | 40 | $0.02 | $0.68 | $0.68 | $44.17 | 2600 | 3300 | $56.07 | 4500 | - |  | 4000 | Mouser
Capacitor – 22u | Digikey Chip1stop | CL32B226KAJNFNE (existing) MCAST32MSB7226KPNA01 (AECQ200) CGA6P3X7R1E226M250AE (soft term) | 9 | 9 | $0.27 | $2.43 | $2.43 | $157.95 | 585 | 500 | $135.00 | 760 | - | 0 | 1000 | DigiKey
PFET | Digikey | RSC002P03T316 (original) NX3008PBK,215 (Vgs=8V) | 62 | 62 | $0.05 | $3.14 | $3.14 | $203.92 | 4030 | 7900 | $399.74 | 6880 | - |  | 3000 | Arrow
LED – GRN | Digikey | LTST-C171GKT | 11 | 11 | $0.05 | $0.52 | $0.52 | $33.94 | 715 | 300 | $14.24 | 2300 | - | 0 | 3000 | Arrow
NFET | Digikey | SSM3K329R (EOL 2025JUN30) IRLML2060TRPBF NXV55UNR | 13 | 13 | $0.10 | $1.29 | $1.29 | $83.66 | 845 | 2400 | $237.60 | 1250 | - |  | 0
NPN | Digikey | BCP56-16T1G | 5 | 5 | $0.18 | $0.89 | $0.89 | $58.05 | 325 | 675 | $120.56 | 865 | - |  | 0
Thermistor – 10k | Digikey | SDNT2012X103F3950FTF NT08104F3950B1F ($) | 5 | 5 | $0.12 | $0.61 | $0.61 | $39.59 | 325 | 550 | $66.99 | 1240 | - |  | 1000
Diode – Flyback | Digikey | 1N4148WRHG | 4 | 4 | $0.04 | $0.15 | $0.15 | $9.88 | 260 | 1700 | $64.60 | 1200 | - |  | 0
Diode – Charger | Digikey | S12MCV7G | 1 | 1 | $0.59 | $0.59 | $0.59 | $38.61 | 65 | 150 | $89.10 | 135 | - |  | 0
OpAmp | Digikey | LT1797CS5 | 1 | 1 | $1.80 | $1.80 | $1.80 | $117.00 | 65 | 172 | $309.60 | 87 | - |  | 0
RS485 | Arrow | LTC1487CS8 | 2 | 2 | $3.66 | $7.32 | $7.32 | $475.80 | 130 | 148 | $541.68 | 157 | - |  | 140 | Arrow
Diode – 5V Zener | Digikey | MMSZ5233B-TP | 1 | 1 | $0.10 | $0.10 | $0.10 | $6.72 | 65 | 530 | $54.80 | 285 | - |  | 0
isoSPI Controller | Mouser | LTC6820HMS | 1 | 1 | $6.21 | $6.21 | $6.21 | $403.65 | 65 | 215 | $1,335.15 | 157 | - |  | 0
Cell BMS | LT Direct | LTC6804IG-2 (old) LTC6811IG-2#3ZZPBF (new) | 5 | 5 | $11.20 | $56.00 | $56.00 | $3,640.00 | 325 | 897 | $10,046.40 | 564 | - |  | 0
Buck Converter | Digikey | AP63205WU | 1 | 1 | $0.66 | $0.66 | $0.66 | $43.03 | 65 | 350 | $231.70 | 291 | - |  | 0
Inductor – 4.7 uH | Digikey | SLF7045T-4R7M2R1-H (EOL) | 1 | 1 | $0.88 | $0.88 | $0.88 | $57.13 | 65 | 128 | $112.50 | 61 | 0.5400 |  | 0
Capacitor – 220u | Digikey | UCL1V221MCL6GS | 3 | 3 | $0.35 | $1.04 | $1.04 | $67.51 | 195 | 294 | $101.79 | 670 | 1.0100 |  | 500 | DigiKey
Triac (RevD) | Digikey | BTA316B-600C,118 | 1 | 1 | $0.89 | $0.89 | $0.89 | $57.85 | 65 | 23 | $20.47 | 74 | 1.5300 | 0 | 120 | Mouser
Triac Driver | Digikey | MOC3023S | 1 | 1 | $0.26 | $0.26 | $0.26 | $17.19 | 65 | 196 | $51.82 | 130 | 0.3400 |  | 0
isoSPI Transformer | Digikey | 7490100111A | 3 | 3 | $2.78 | $8.34 | $8.34 | $542.10 | 195 | 149 | $414.22 | 197 | 0.7100 | 0 | 275 | DigiKey
optoIsolator | Digikey Newark | SFH620A-2X007T | 2 | 2 | $0.66 | $1.31 | $1.31 | $85.41 | 130 | 471 | $309.45 | 242 | 0.2300 |  | 0
MCMe isolation | Digikey | H11D1SR2VM | 1 | 1 | $0.59 | $0.59 | $0.59 | $38.11 | 65 | 63 | $36.94 | 97 | 0.4400 | 0 | 100 | Verical
DCDC Ferrites | Digikey | MAKK2016T1R0M | 2 | 2 | $0.10 | $0.20 | $0.20 | $13.26 | 130 | 145 | $14.79 | 243 | - |  | 250 | oc
 |  |  |  |  | Section Subtotal | $112.66 | $112.66 | $7,322.91 |  |  | $15,580.14
 |  |  |  |  | Subtotal To Here | $112.66 | $112.66 | $7,322.91 |  |  | $15,580.14
SMT Hand Placed
Conn-Temp Sensor, SMT | Mouser | 5055680281 | 3 | 3 | $0.42 | $1.27 | $1.27 | $82.76 | 195 | 220 | $93.37 | 219 | 0.1200 |  | 200 | DigiKey
Slide Switch (DIP) | Digikey | 219-2LPSTR | 1 | 1 | $0.42 | $0.42 | $0.42 | $26.97 | 65 | 0 | $0.00 | 78 | - | 0 | 150 | Mouser
Triac Heatsink | Digikey | DV-T263-301E-TR | 1 | 1 | $1.80 | $1.80 | $1.80 | $117.00 | 65 | 31 | $55.80 | 75 | 5.7500 | 0 | 110 | DigiKey
 |  |  |  |  | Section Subtotal | $3.49 | $3.49 | $226.73 |  |  | $149.17
 |  |  |  |  | Subtotal To Here | $116.15 | $116.15 | $7,549.64 |  |  | $15,729.31
Thru Hole
HVDC→DC (RevD) | OnlineComponents | EPM1510SJ (RevD) | 1 | 1 | $5.92 | $5.92 | $5.92 | $384.80 | 18 | 133 | $787.36 | 70 | - |  | 0
BCM Connector | Newark | 174917-6 | 1 | 1 | $10.62 | $10.62 | $10.62 | $690.30 | 65 | 30 | $318.60 | 76 | - | 0 | 110 | Newark
Capacitor – Bulk HVDC | Digikey | URY2F330MRD (33 uF)(EOL) URY2G220MRD (22 uF)(EOL) UCY2G330MHD3 (proposed RevE) | 1 | 1 | $1.50 | $1.50 | $1.50 | $97.81 | 65 | 111 | $167.03 | 49 | - |  | 0 0 1 | DigiKey
Fuse Holder | Digikey | 0031.8201 | 2 | 2 | $0.61 | $1.22 | $1.22 | $79.04 | 130 | 81 | $49.25 | 292 | 1.5400 | 0 | 400 | Arrow
Screw Terminal – 8p (HVDC) | Digikey | A98163-ND | 1 | 1 | $3.74 | $3.74 | $3.74 | $243.10 | 65 | 65 | $243.10 | 101 | 5.9100 |  | 100 | oc
Screw Terminal – 8p (Fans) | Mouser | 277-1725-ND | 1 | 1 | $2.02 | $2.02 | $2.02 | $131.30 | 65 | 285 | $575.70 | 221 | 3.7400 |  | 0
0.1” 1x8 (8p) | Arrow | WM24407-ND | 8 | 8 | $0.31 | $2.46 | $2.46 | $159.64 | 520 | 420 | $128.94 | 865 | 0.4700 | 0 | 1000 | DigiKey
0.1” 2x9 (18p)(new) | Digikey | S2011E-09-ND | 1 | 1 | $0.87 | $0.87 | $0.87 | $56.49 | 65 | 42 | $36.50 | 77 | 1.0200 | 0 | 100 | DigiKey
20P Ribbon Header, RA, locking | Digikey | 609-86130202113345E1LF-ND | 1 | 1 | $0.70 | $0.70 | $0.70 | $45.24 | 65 | 79 | $54.98 | 194 | - |  | 180 | Newark
20P Ribbon Header, Straight | Digikey | SBH11-PBPC-D10-ST-BK | 1 | 1 | $0.39 | $0.39 | $0.39 | $25.48 | 65 | 49 | $19.21 | 135 | 2.4400 | 0 | 150 | DigiKey
14P Ribbon Header, RA, locking | Digikey | AWH14A-0232-T-R (obsolete) MHR-14-HUAL 3010-14-002-13-00 (new) | 2 | 7 | $0.49 | $0.99 | $3.45 | $64.09 | 130 | 19 | $9.37 | 184 | - | 0 | 571 | Verical
LiDisplay 1x4 Header, RA | Digikey | 2057-CDR-04-GR-ND | 1 | 1 | $0.18 | $0.18 | $0.18 | $11.96 | 65 | 24 | $4.42 | 84 | 0.9200 | 0 | 125 | DigiKey
Cover Switch (Cherry) | Arrow | MX1A-11NW | 1 | 1 | $0.80 | $0.80 | $0.80 | $52.00 | 65 | 24 | $19.20 | 60 | 1.6300 | 5 | 100 | Mouser
Buzzer | Digikey | 433-1028-ND | 1 | 1 | $0.38 | $0.38 | $0.38 | $24.70 | 65 | 32 | $12.16 | 67 | 1.6300 | 0 | 100 | oc
 |  |  |  |  | Section Subtotal | $31.78 | $34.25 | $2,065.95 |  |  | $2,425.81
 |  |  |  |  | Subtotal To Here | $147.93 | $150.40 | $9,615.59 |  |  | $18,155.12
Other Parts Attached to PCB
Fan | OnlineComponents Sager | MF60151VX-1000U-A99 | 3 | 4 | $5.44 | $16.32 | $21.76 | $1,060.80 | 195 | 162 | $881.28 | 200 | - | 0 | 320
Fuse AC | Digikey | 0ADKC8000-BE | 1 | 1 | $0.83 | $0.83 | $0.83 | $53.76 | 65 | 75 | $62.03 | 111 | 1.3700 |  | 100 | Mouser
Fuse DC | Digikey | 0ADKC6300-BE | 1 | 1 | $0.88 | $0.88 | $0.88 | $57.20 | 65 | 311 | $273.68 | 252 | 1.3500 |  | 0
Arduino Mega2560 | Amazon Elegoo | Clone | 1 | 1 | $21.99 | $21.99 | $21.99 | $1,429.35 | 65 | 38 | $835.62 | 95 | - | 0 | 64
M3x6 screw, self tapping (BCM conn) | McMaster | 90380A348 | 3 | 3 | $0.07 | $0.20 | $0.20 | $13.07 | 195 | 88 | $5.90 | 293 | 0.4200 | 0 | 400
DANGER Label | Digikey | 298-18583-ND | 1 | 2 | $0.19 | $0.19 | $0.39 | $12.59 | 65 | 150 | $29.06 | 150 | - |  | 0
M4 washer | McMaster Amazon | 93475A230 | 12 | 20 | $0.03 | $0.30 | $0.50 | $19.50 | 780 | 1559 | $38.98 | 700 | 0.2500 |  | 1000
M4-0.7x10 button head bolt | Amazon |  | 9 | 7 | $0.09 | $0.81 | $0.63 | $52.59 | 585 | 244 | $21.94 | 378 | 1.3700 | 207 | 800
M4-0.7x25 button head bolt | Amazon |  | 12 | 12 | $0.10 | $1.26 | $1.26 | $81.82 | 780 | 236 | $24.76 | 891 | 2.4400 | 0 | 1500
Plastic M4 Washer (RED) | Digikey | RPC3441-ND (obsolete) | 12 | 12 | $0.08 | $0.95 | $0.95 | $61.62 | 780 | 3380 | $267.02 | 2720 | 0.0450 |  | 0
M4 Lock Nut | Amazon |  | 7 | 9 | $0.05 | $0.35 | $0.45 | $22.75 | 455 | 235 | $11.75 | 1164 | 0.8000 | 0 | 1200
Standoff – M4-0.7x25 Switch | Digikey | 952-1543-ND | 1 | 1 | $0.51 | $0.51 | $0.51 | $33.15 | 65 | 11 | $5.61 | 57 | 6.7000 | 8 | 150 | Mouser
Standoff – M4-0.7x20 Cover | Digikey | 952-1542-ND | 5 | 5 | $0.44 | $2.19 | $2.19 | $142.03 | 325 | 179 | $78.22 | 379 | 5.2000 | 0 | 525 | Mouser
Polycarbonate Safety Cover | Hall Precision | LiBCM-001 | 1 | 1 | $27.50 | $27.50 | $27.50 | $1,787.50 | 65 | 15 | $412.50 | 68 | - | 0 | 250
 |  |  |  |  | Section Subtotal | $74.27 | $80.03 | $4,827.73 |  |  | $2,948.33
 |  |  |  |  | Subtotal To Here | $222.20 | $230.42 | $14,443.32 |  |  | $21,103.45
Other Items Included with PCB Purchase
5AhG3 Aluminum Mounting Plate | EVS | JTS-LiBCM-001 | 3 | 0 | $9.05 | $27.15 | $0.00 | $1,764.75 | 195 | 224 | $2,027.20 | 183 | - |  | 0
HVDC Ferrite Core | Digikey | 2631626202 | 1 | 1 | $8.78 | $8.78 | $8.78 | $570.70 | 65 | 110 | $965.80 | 120 | - |  | 48 | oc
Wire – 18 AWG (RED) | Digikey | CN512R-500-ND‎ | 2.5 | 2.5 | $0.27 | $0.67 | $0.67 | $43.71 | 162.5 | 100 | $26.90 | 170 | - | 0 | 600 | DigiKey
Wire – 18 AWG (BLK) | Digikey | CN548B-500-ND | 2.5 | 2.5 | $0.27 | $0.67 | $0.67 | $43.71 | 162.5 | 120 | $32.28 | 1000 | - | 0 | 500 | DigiKey
Wire – 18 AWG (WHT) | Digikey | CN549W-100-ND | 1 | 3 | $0.27 | $0.27 | $0.81 | $17.49 | 65 | 530 | $142.57 | 530 | - |  | 0
Wire – 18 AWG (GRN) | Digikey | CN557GY-100-ND (discontinued) CN554G-500-ND (new) | 1 | 1 | $0.27 | $0.27 | $0.27 | $17.49 | 65 | 510 | $137.19 | 475 | - |  | 0
Adhesive Shipping Label | Amazon |  | 1 | 1 | $0.05 | $0.05 | $0.05 | $3.25 | 65 |  | $0.00 |  | - | 65 | 0
Foam Sleeve | U-Line | S-1560 | 1 | 0 | $0.35 | $0.35 | $0.00 | $22.75 | 65 | 27 | $9.45 | 27 | - | 38 | 0
Cardboard Box | Amazon | 24x12x4 | 1 | 0 | $2.34 | $2.34 | $0.00 | $152.10 | 65 | 22 | $51.48 | 14 | - | 51 | 0
Cardboard Box | U-Line | S-23983 20x8x3 (20.5*8.5*3.5 OD) | 1 | 1 | $1.98 | $1.98 | $1.98 | $128.70 | 65 | 15 | $29.70 | 126 | - | 0 | 135
Shipping (UPS) | UPS | Insured for $1200 | 1 | 2 | $30.00 | $30.00 | $60.00 | $1,950.00 |  | - | - | - | - |  | 0
 |  |  |  |  | Section Subtotal | $72.53 | $73.23 | $4,714.64 |  |  | $3,422.57
 |  |  |  |  | Subtotal To Here | $294.74 | $303.65 | $19,157.96 |  |  | $24,526.02
Grid Charger
IEC cord (10A) | Digikey | Q106-ND | 1 | 1 | $4.33 | $4.33 | $4.33 | $281.71 | 65 | 6 | $26.00 | 107 | - | 0 | 125 | DigiKey
Grid Charger | Digikey chip1stop | PLED96W-213-C0450-D (old) XLG-150-L-AB (new) | 1 | 0 | $34.31 | $34.31 | $0.00 | $2,230.15 | 65 | 64 | $2,195.84 | 64 | - | 1 | 0
Grid Charger | Digikey chip1stop | HLG-480H-C2100B | 0.05 | 0.5 | $142.90 | $7.15 | $71.45 | $464.42 | 3.25 | 4 | $571.60 | 0 | - |  | 20 | Verical
Grid Charger Standoff | Digikey | 1772-1243-ND 1772-3419-ND (more expensive) | 0.1 | 0 | $0.69 | $0.07 | $0.00 | $4.49 | 6.5 | 49 | $33.81 | 48 | 2.3400 |  | 0
Anderson Roll Pin 3/32x0.5” | McMaster | 98296A841 | 2 | 6 | $0.27 | $0.53 | $1.59 | $34.45 | 130 | 90 | $23.85 | 190 | 0.2800 | 0 | 500
½" Conduit (non-slit) | electriduct.com | WL-PP-NS-050 | 0.3 | 0 | $0.34 | $0.10 | $0.00 | $6.63 | 19.5 | 148 | $50.31 | 120 | - |  | 0
M4 T-slot Nut | Fairway Fasteners | JPPNM04016 | 4 | 0 | $0.15 | $0.59 | $0.00 | $38.17 | 260 | 123 | $18.06 | 192 | 2.4200 | 68 | 100
 |  |  |  |  | Section Subtotal | $47.08 | $77.37 | $3,060.02 |  |  | $2,919.47
 |  |  |  |  | Subtotal To Here | $341.82 | $381.03 | $22,217.98 |  |  | $27,445.49
4 AWG Cables
Anderson - 75A contact (6AWG) | Powerwerx | 5900-BK | 2 | 3 | $0.93 | $1.86 | $2.79 | $120.90 | 130 | 15 | $13.95 | 88 | 4.3300 | 42 | 100
Anderson – 75A RED Housing | Powerwerx | 5916G7-BK | 1 | 0 | $1.14 | $1.14 | $0.00 | $74.10 | 65 | 56 | $63.84 | 30 | 7.1000 | 35
Anderson – 75A BLU Housing | Powerwerx | 5916-BK | 0 | 3 | $1.14 | $0.00 | $3.42 | $0.00 | 0 | 9 | $10.26 | 5 | 7.1000 |  | 20
Anderson – 75A BLK Housing | Powerwerx | 5916G4-BK | 1 | 0 | $1.08 | $1.08 | $0.00 | $70.20 | 65 | 7 | $7.56 | 49 | 7.1000 | 16 | 10
Ring – Batteries | Avnet | A27073-ND (existing) WM19129-ND (TBD) A27083-ND (meh) 277-11172-ND (meh) | 6 | 11 | $0.49 | $2.93 | $5.38 | $190.71 | 390 | 72 | $35.21 | 184 | 5.6000 | 206 | 300 | tti
Ring – Fuse/Switch | Digikey | 277-11168-ND | 2 | 2 | $0.55 | $1.10 | $1.10 | $71.76 | 130 | 0 | $0.00 | 57 | 4.2000 | 73 | 100 | oc
Ring – Relay/HVDC- | Digikey | A112030-ND (existing)(best) 23-0191930245-ND (works, thinner)(better) A27067-ND (works, narrower)(good) | 2 | 2 | $1.07 | $2.15 | $2.15 | $139.67 | 130 | 17 | $18.26 | 56 | 5.3000 | 74 | 100 | oc
3/8" Conduit (non-slit) | electriduct.com | WL-PP-NS-0375 | 6 | 10 | $0.37 | $2.19 | $3.65 | $142.35 | 390 | 700 | $255.50 | 600 | - |  | 0
Current Cables 4AWG | Ebay seller Acdcwireandsupply Search: “excelene #4 500” thewireszone,com | Southwire Royal Excelene #4 – 500’ Radnor #4 FP4167 Direct #4 Flex-A-Prene FP0951 Direct #4 Flex-A-Prene FP4-B50RD | 7.5 | 11.2 | $1.49 | $11.18 | $16.69 | $726.38 | 487.5 | 16 | $23.84 | 505 | - | 0 | 250
½” Heat Shrink | Amazon | ½" heat shrink | 5 | 0 | $0.07 | $0.35 | $0.00 | $22.75 | 325 | 168 | $11.76 | 12 | - | 313 | 0
 |  |  |  |  | Section Subtotal | $23.98 | $35.18 | $1,558.82 |  |  | $440.18
 |  |  |  |  | Subtotal To Here | $365.80 | $416.21 | $23,776.79 |  |  | $27,885.67
BMS Cables
18S Connector (Honda) | yghaidie.com | HD281-0.7-2.2-21J | 2 | 0 | $2.12 | $4.24 | $0.00 | $275.60 | 130 | 194 | $411.28 | 167 | 8.7500 |  | 0
12S Connector (Honda) | yghaidie.com | HD202-0.7-11J (6098-4595) | 1 | 0 | $2.26 | $2.26 | $0.00 | $146.90 | 65 | 312 | $705.12 | 394 | 5.8300 |  | 0
20P Ribbon Cable | Digikey | MC20M-25-ND 3M157940-100-ND | 1 | 2 | $1.33 | $1.33 | $2.66 | $86.50 | 65 | 5 | $6.65 | 38 | - | 27 | 200 | tti
14P Ribbon Cable | Digikey | MC14M-25-ND | 0.5 | 0 | $0.99 | $0.49 | $0.00 | $32.12 | 32.5 | 25 | $24.71 | 21 | - | 11.5 | 0
20P Ribbon Connector | Digikey | SFH213-PPPC-D10-ID-BK 71600-020LF | 2 | 2 | $0.66 | $1.32 | $1.32 | $85.80 | 130 | 88 | $58.08 | 98 | 2.7000 | 32 | 230 | DigiKey
14P Ribbon Connector | Digikey | SFH213-PPPC-D07-ID-BK 3030-14-0103-00 71600-014LF | 1 | 7 | $0.66 | $0.66 | $4.63 | $43.03 | 65 | 44 | $29.13 | 100 | 2.0000 | 0 | 600 | DigiKey
Ribbon Cable Sleeving | Cabletiesandmore | F6Z1.00-50 (TechFlex F6 Flat 1") | 0.4 | 1 | $1.31 | $0.52 | $1.31 | $34.06 | 26 | 40 | $52.40 | 38 | -
18S ferrule (large pins) | Digikey Digikey Amazon | 288-1077-ND (short) 288-1078-ND (long) Tnisesm 26-22 non-insulated butt | 4 | 0 | $0.04 | $0.18 | $0.00 | $11.44 | 260 | 511 | $22.48 | 131 | 0.0280 |  | 0
 |  |  |  |  | Section Subtotal | $11.01 | $9.93 | $715.46 |  |  | $1,309.86
 |  |  |  |  | Subtotal To Here | $376.80 | $426.13 | $24,492.25 |  |  | $29,195.53
4x20 Display
LCD | Amazon | 4x20 with I2C | 1 | 1 | $7.10 | $7.10 | $7.10 | $461.50 | 65 | 9 | $63.90 | 37 | - | 28 | 90
Berg Housing - 1x4 | Digikey | 65039-033ELF 65039-033LF | 2 | 2 | $0.18 | $0.36 | $0.36 | $23.53 | 130 | 76 | $13.76 | 234 | 0.1800 | 0 | 250 | Arrow
Berg contact - 28 AWG | Digikey | 48249-000LF | 4 | 4 | $0.13 | $0.52 | $0.52 | $33.97 | 260 | 86 | $11.24 | 392 | 0.0730 | 0 | 500 | Arrow
Berg contact - 24 AWG | Digikey | 48248-000LF | 4 | 4 | $0.13 | $0.52 | $0.52 | $33.97 | 260 | 92 | $12.02 | 200 | 0.0830 | 60 | 300 | Arrow
Shielded Cable | Digikey | CN308-1000-ND | 10 | 10 | $0.24 | $2.42 | $2.42 | $157.30 | 650 | 0 | $0.00 | 530 | - | 120 | 1000 | DigiKey
¼” Heat shrink | Amazon | 1/4" | 2 | 2 | $0.02 | $0.04 | $0.04 | $2.60 | 130 | 36 | $0.72 | - | - |  | 0
VHB Adhesive | Amazon | LSE-160WF 2" wide | 1 | 1 | $0.19 | $0.19 | $0.19 | $12.61 | 65 | 100 | $19.39 | 500 | - |  | 0
 |  |  |  |  | Section Subtotal | $11.16 | $11.16 | $725.47 |  |  | $121.03
 |  |  |  |  | Subtotal To Here | $387.96 | $437.30 | $25,217.72 |  |  | $29,316.56
Other Electronics
Batt temp sensor - short | Digikey | 900-2138651635-ND | 3 | 1 | $2.52 | $7.55 | $2.52 | $490.82 | 195 | 204 | $513.47 | 46 | - |  | 0
USB Cable A→B | Digikey | AE10618-ND | 1 | 1 | $2.46 | $2.46 | $2.46 | $159.90 | 65 | 39 | $95.94 | 27 | - | 38 | 100 | DigiKey
Grid Charger/VPIN | Powerwerx | Anderson - 15A contact | 9 | 17 | $0.18 | $1.62 | $3.06 | $105.30 | 1177 | 1373 | $247.14 | 500 | 0.4800 |  | 2000
Grid Charger | Powerwerx | Anderson - 30A contact | 4 | 4 | $0.17 | $0.68 | $0.68 | $44.20 | 460 | 360 | $61.20 | 1118 | 0.6000 | 0 | 500
Grid Charger | Powerwerx | Anderson – GRN | 2 | 2 | $0.34 | $0.68 | $0.68 | $44.20 | 230 | 451 | $153.34 | 168 | 1.1000 |  | 0
Grid Charger/VPIN LiBCM PCB HVDC- | Powerwerx | Anderson – WHT | 4 | 6 | $0.44 | $1.76 | $2.64 | $114.40 | 508 | 877 | $385.88 | 507 | 1.1000 |  | 400
Grid Charger | Powerwerx | Anderson – BLK | 2 | 8 | $0.42 | $0.84 | $3.36 | $54.60 | 230 | 98 | $41.16 | 585 | 1.1000 | 0 | 1000
Grid Charger/VPIN | Powerwerx | Anderson – ORG | 4 | 4 | $0.44 | $1.76 | $1.76 | $114.40 | 408 | 33 | $14.52 | 514 | 1.1000 | 0 | 1000
Ring terminal – M4 18AWG | Digikey | 277-11146-ND | 2 | 2 | $0.10 | $0.19 | $0.19 | $12.48 | 130 | 457 | $43.87 | 74 | 0.6000 |  | 0
Screw terminal ferrule, 20 AWG | Amazon | GRY – E7508 | 6 | 6 | $0.02 | $0.10 | $0.10 | $6.63 | 390 | 370 | $6.29 | 1500 | - | 0 | 1000
Screw terminal ferrule, 22 AWG | Amazon | WHT – E0508 |  |  | $0.02 |  |  |  |  | 75 | $1.50 | 900 | - |  | 1000
Screw terminal ferrule, 18 AWG | Amazon | RED – E1008 | 2 | 0 |  |  |  |  |  | 70 | $0.00 | 70 | - |  | 0
Wire nut – GRY | Amazon | - | 2 | 2 | $0.01 |  |  |  |  | 516 | $5.16 | 164 | 0.3900 |  | 0
Conduit – 1/8” (LiBCM power and temp sensors) | Amazon (EOL) Ebay? sherco-auto.com? | 1/8" conduit | 4 | 5 | $0.30 | $1.20 | $1.50 | $78.00 | 260 | 560 | $168.00 | 120 | - |  | 0
Conduit – ¼” OD, non-slit | Electriduct | WL-PP-NS-025-100-BK | 1 | 1 | 0.24 | $0.24 | $0.24 | $15.60 |  | 290 | $69.60 | 10 | - |  | 0
Conduit – ¼” ID, non-slit (MCM'E' & Grid harness) | Electriduct.com | WL-BK-NS-025-100 | 1.43 | 3 | $0.24 | $0.34 | $0.72 | $22.26 | 92.77 | 230 | $55.20 | 70 | - |  | 100
 |  |  |  |  | Section Subtotal | $19.43 | $19.91 | $1,262.79 |  |  | $1,862.27
 |  |  |  |  | Subtotal To Here | $407.39 | $457.21 | $26,480.51 |  |  | $31,178.83
Other Hardware
M6x1 Nut (Battery) | McMaster | 97400A101 | 6 | 7 | $0.18 | $1.08 | $1.26 | $70.20 | 390 | 368 | $66.24 | 237 | 3.1000 | 153 | 600
M8 Washer | McMaster | 98689A116 | 6 | 0 | $0.07 | $0.43 | $0.00 | $28.08 | 390 | 676 | $48.67 | 614 | 1.1800 |  | 0
M8-1.25x40 Standoff | Amazon | 5AhG3 12S standoff | 2 | 0 | $1.40 | $2.80 | $0.00 | $182.00 | 130 | 85 | $119.00 | 65 | 20.9000 | 65 | 0
M8-1.25 Nut (stainless) | Amazon | 5AhG3 12S standoff | 2 | 0 | $0.08 | $0.16 | $0.00 | $10.37 | 130 | 0 | $0.00 | 0 | - | 130 | 0
M8-1.25 Nut (zinc) | McMaster | 90591A161 | 4 | 0 | $0.20 | $0.80 | $0.00 | $52.00 | 260 | 525 | $105.00 | 486 | 4.5000 |  | 0
M8-1.25x12 mm Bolt | McMaster | 91280A524 | 2 | 0 | $0.36 | $0.72 | $0.00 | $46.80 | 130 | 266 | $95.76 | 247 | 9.1000 |  | 0
Adhesive Thermal Labels | Amazon | TZe231 12mm BLKonWHT & BLKonCLR | 0.13 | 0.25 | $3.00 | $0.37 | $0.75 | $24.35 | 8.13 | 10 | $29.98 | 400 | - |  | 0
Edge Trim (power cable) GRY | Amazon | uxcell 1/64:1/16" U channel | 0.36 | 0.36 | $1.25 | $0.45 | $0.45 | $29.23 | 23.4 | 11 | $13.74 | 37 | 8.0000 | 0 | 40
Flat head screwdriver | Amazon | 2.0 mm flat head | 1 | 1 | $0.34 | $0.34 | $0.34 | $22.09 | 65 | 51 | $17.33 | 37 | 3.3000 | 28 | 50
Allen Wrench | Amazon | 2.5 mm L | 1 | 1 | $0.35 | $0.35 | $0.35 | $22.75 | 65 | 37 | $12.95 | 42 | - | 23 | 120
Ziplock bag (parts kit) | Amazon | 6x9 | 1 | 1 | $0.10 | $0.10 | $0.10 | $6.25 | 65 | 72 | $6.93 | 45 | - |  | 200
Zip tie - 4" | Home Depot |  | 8 | 8 | $0.02 | $0.16 | $0.16 | $10.40 | 520 | 300 | $6.00 | 400 | - | 120
Zip tie - 8" | Home Depot |  | 5 | 2 | $0.02 | $0.10 | $0.04 | $6.50 | 325 | 950 | $19.00 | 800 | - |  | 0
 |  |  |  |  | Section Subtotal | $7.86 | $3.45 | $511.03 |  |  | $540.59
 |  |  |  |  | Subtotal To Here | $415.25 | $460.65 | $26,991.54 |  |  | $31,719.42
FoMoCo Parts
EPDM Module Adhesive Rubber Insulator | Rubbersheetwarehouse Amazon (cheaper) | 4x10" 60A Rubber 0.031" with adhesive 10' roll | 0 | 5 | $5.00 | $0.00 | $25.00 | $0.00 | 0 | 33 | $165.00 | 0 | - |  | 250
Bolt, stainless, 3.75" ¼"-20 | McMaster Amazon | 92198A557 https://www.amazon.com/Hex-Screws-18-8-Stainless-Steel/dp/B00FATYT94 | 0 | 12 | $0.54 | $0.00 | $6.44 | $0.00 | 0 | 16 | $8.59 | 135 | 25.2000 |  | 1200
Bolt, 5" ¼"x20 | McMaster Amazon | 91236A562 9058745 | 0 | 8 | $0.38 | $0.00 | $3.02 | $0.00 | 0 | 10 | $3.77 | 0 | - |  | 800
Washer, stainless, ¼" | McMaster | 92141A029 | 0 | 12 | $0.03 | $0.00 | $0.42 | $0.00 | 0 | 170 | $5.90 | 246 | 1.5900 |  | 1100
Grid Charger Aluminum Tray | EVS | LIBCM-005 | 0 | 1 | $11.25 | $0.00 | $11.25 | $0.00 | 0 | 106 | $1,192.50 | 8 | - |  | 0
PEMSERT ¼” | Amazon McMaster | CLS-0420-2 0.250-20 | 0 | 4 | $0.34 | $0.00 | $1.35 | $0.00 | 0 | 393 | $132.83 | 99 | 2.8600 |  | 45
Aluminum Bracket - 1x1x18.125” @ 0.125” wall | EVS | LiBCM-004 | 0 | 2 | $33.95 | $0.00 | $67.90 | $0.00 | 0 | 197 | $6,688.15 | 1 | - |  | 0
Heat shrink ¼" | Digikey | DWP014K-ND ES2000-NO.1-C1-0-STK-ND | 0 | 4 | $0.16 | $0.00 | $0.64 | $0.00 | 0 | 240 | $38.43 | 28 | - |  | 0
Heat shrink 3/16" | Digikey | DWP316K-ND | 0 | 3 | $0.13 | $0.00 | $0.38 | $0.00 | 0 | 432 | $55.22 | 0 | - |  | 0
14P Ribbon Cable - Insulated | Digikey | MB14J-100-ND | 0 | 4.3 | $2.06 | $0.00 | $8.86 | $0.00 | 0 | 0 | $0.00 | 43 | - |  | 413 | DigiKey
Resistor – 8k25 | Digikey | RMCF1206FT8K25CT-ND | 0 | 2 | $0.01 | $0.00 | $0.01 | $0.00 | 0 | 950 | $5.70 | 500 | - |  | 0
Resistor – 13k3 | Digikey | RHM13.3KCJCT-ND | 0 | 2 | $0.01 | $0.00 | $0.01 | $0.00 | 0 | 950 | $4.94 | 500 | - |  | 0
2 conductor Cable 22AWG | Digikey | BEL1080-100-ND | 0 | 2 | $0.48 | $0.00 | $0.97 | $0.00 | 0 | 200 | $96.62 | 80 | - |  | 0
Blue Hookup Wire | Digikey | CN513L-100-ND | 0 | 2 | $0.27 | $0.00 | $0.54 | $0.00 | 0 | 40 | $10.76 | 60 | - |  | 100 | DigiKey
IMA top cover felt | Amazon | Pllieay 2"x0.04x14.7 feet | 0 | 4 | $0.48 | $0.00 | $1.90 | $0.00 | 0 | 140 | $66.57 | 40 | - |  | 280
Round Felt Pads | Amazon | 32mm (1.25") round 2mm | 0 | 8 | $0.21 | $0.00 | $1.67 | $0.00 | 0 | 13 | $2.71 | 39 | 0.6600 |  | 816
PCB – Samsung SDI Module | JLCPCB | - | 0 | 5 | $2.48 | $0.00 | $12.42 | $0.00 | 0 | 31 | $77.02 | 14 | - |  | 250
Lower Aluminum Tray | EVS | LIBCM-003 | 0 | 1 | $41.65 | $0.00 | $41.65 | $0.00 | 0 | 109 | $4,539.85 | 1 | - |  | 0
Al ¼" Spacer 1"OAL | AluminumSpacers.com Amazon | 501614RSA (Amazon) AS50-14-64 | 0 | 8 | $0.36 | $0.00 | $2.88 | $0.00 | 0 | 128 | $46.08 | 704 | 6.4000 |  | 1000
Spade Terminal for PDU Fan | Digikey | 298-16678-ND (old) | 0 | 2 | $0.31 | $0.00 | $0.61 | $0.00 | 0 | 0 | $0.00 | 36 | - |  | 250 | DigiKey
¼"-20 x ½" bolt, phillips (MCM) | Mcmaster | 91770A537 | 0 | 4 | $0.26 | $0.00 | $1.04 | $0.00 | 0 | 3 | $0.78 | 52 | 5.2000 |  | 250
¼”x1.5” Standoff (MCM) | Digikey | 1772-1622-ND | 0 | 2 | $1.81 | $0.00 | $3.63 | $0.00 | 0 | 0 | $0.00 | 150 | 32.8000 |  | 212 | DigiKey
M8x16x1.25 bolt - Tray | Amazon | DIN6921 M8x16 | 0 | 4 | $0.46 | $0.00 | $1.84 | $0.00 | 0 | 70 | $32.17 | 50 | 14.7000 |  | 360
¼"-20x1.25" threaded Hex standoff | Digikey | 2317-2520-S-12 | 0 | 8 | $1.73 | $0.00 | $13.84 | $0.00 | 0 | 15 | $25.95 | 33 | 27.5000 |  | 835 | DigiKey
M4x12 countersunk DIN7991 | Amazon |  | 0 | 4 | $0.09 | $0.00 | $0.38 | $0.00 | 0 | 0 | $0.00 | 8 | - |  | 400
LiBCM PCB HVDC+ | Powerwerx | Anderson – RED | 0 | 6 | $0.42 | $0.00 | $2.52 | $0.00 | 0 | 138 | $57.96 | 203 | 1.1000 |  | 500
Grid Temp Sensor | Powerwerx | Anderson – BLU | 0 | 5 | $0.44 | $0.00 | $2.20 | $0.00 | 0 | 215 | $94.60 | 40 | 1.1000 |  | 400
Positap 20-22 AWG | Amazon | ZB-PTA2022R | 0 | 2 | $0.98 | $0.00 | $1.97 | $0.00 | 0 | 43 | $42.31 | 333 | 1.5000 |  | 500
M4x0.7 30mm threaded shaft | Amazon | uxcell | 0 | 4 | $0.21 | $0.00 | $0.86 | $0.00 | 0 | 53 | $11.34 | 303 | 2.2000 |  | 350
M4 nut - non-captive | Amazon | uxcell | 0 | 8 | $0.03 | $0.00 | $0.27 | $0.00 | 0 | 124 | $4.13 | 797 | 0.6700 |  | 900
ORG battery terminal cover, 3DP | @mario |  | 0 | 5 | $0.60 | $0.00 | $3.00 | $0.00 | 0 | 174 | $104.40 | 221 | 2.3900
electric tape – Black | Home Depot | 6132-BA-3PK-6 | 0 | 1 | $4.44 | $0.00 | $4.44 | $0.00 | 0 | 6 | $26.63 | 5 | - |  | 90
FoMoCo box 22x22x8 | Uline | S-4651 | 0 | 1 | 3.61 | $0.00 | $3.61 | $0.00 | 0 | 101 | $364.61 | 54 | - |  | 0
FoMoCo box 20x18x6 | Uline | S-4903 | 0 | 1 | 2.66 | $0.00 | $2.66 | $0.00 | 0 | 95 | $252.70 | 101 | - |  | 0
FoMoCo box 12x7x5 | Uline | S-13293 | 0 | 1 | 0.89 | $0.00 | $0.89 | $0.00 | 0 | 100 | $89.00 | 0 | - |  | 0
300x300 mm mica sheet | Amazon | GZFY 300mm x 300mm (EOL?) | 0 | 1 | 5.33 | $0.00 | $5.33 | $0.00 | 0 | 45 | $239.85 | 44 | -
Samsung Module Edge Trim (HVDC) | McMaster | 8693K21 | 0 | 1 | 1.52 | $0.00 | $1.52 | $0.00 | 0 | 16.33 | $24.83 | 0 | - |  | 25
Batt temp sensor - long | Digikey | 900-2138651637-ND | 0 | 2 | $3.76 | $0.00 | $7.52 | $0.00 | 0 | 9 | $33.84 | 65 | - |  | 200 | DigiKey
 |  |  |  |  | Section Subtotal | $0.00 | $245.43 | $0.00 |  |  | $14,545.75
 |  |  |  |  | Subtotal To Here | $415.25 | $706.08 | $26,991.54 |  |  | $46,265.17
 |  |  |  |  |  | $/EHW5 LiBCM: | $/FoMoCo LiBCM:
 |  |  |  |  | BOM | $415.25 | $706.08
 |  |  |  |  | Taxes & Defects | $59.17 | $100.62
 |  |  |  |  | Total COGs | $474.43 | $806.69 | Labor not Included
 |  |  |  |  | Sale Price | $1,250 | $2,000
 |  |  |  |  | profit/ LiBCM | $775.57 | $1,193.31 | Labor not Included
 |  |  |  |  | Total Profit N units | $50,412.17

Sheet: 18S->12S BOM
 |  |  |  |  |  |  |  | 25
How Installed | Where Used | Supplier | Part Number | Component Value | QTY / PCB | $/ Part | $/ LiBCM | $/ QTY n LiBCMs (n=above) | QTY needed For n LiBCMs | 2024DEC QTY on Hand | 2025APR QTY on Hand | grams /unit | $ spent thus far | Additional QTY to order for n PCBs | QTY Ordered | Planning
Standoff | Compress 12S cells into 18S cage | Digikey | 732-10493-ND | M6-1.0x45 | 12 | $1.44 | $17.28 | $432.00 | 300 | 100 | 251 | 28.4000 | 931.68 | 200 | 162 |  | DigiKey
Bolt | Attaches module to aluminum plate | Amazon McMaster | button head 94500A315 | M6-1.0x14 | 3 | 0.36 | $1.08 | $26.97 | 75 | 121 | 110 | 3.7000 | 26.97 |  | 0
Washer | Attaches module to aluminum plate | Amazon | DIN9021 | M6 washer | 3 | 0.12 | $0.35 | $8.85 | 75 | 155 | 143 | 2.3900 | 11.80 |  | 0
Ring terminal |  | Digikey | A111470TR-ND |  | 13 | 0.16 | $2.07 | $51.68 | 325 | 2047 | 2000 | 0.4200 | 397.50 |  | 0
4" zip tie | Harness | Home Depot |  |  | 10 | 0.02 | $0.20 | $5.00 | - | - | - | - | - | -
Ribbon Cable | 14P Cable |  | MC14M-25-ND |  | 1 | 0.99 | $0.99 | $24.71 | - | - | - | - | - | -
Connector | 14P Ribbon Connector |  |  |  | 1 |  | already included in LiBCM BOM |  | - | - | - | - | - | -
 |  |  |  |  |  | BOM $/ LiBCM | 21.97
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

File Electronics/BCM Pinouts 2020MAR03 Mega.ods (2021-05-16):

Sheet: MCM
MCM Pin | Color | OEM MCM Signal Name | OEM Use | OEM Signal Sent From | OEM Signal Sent To | OEM Signal Details | Rdy for Sch? | Schematic name@uC | Atmel Studio #define | IMA OEM pullup/ down resistors | Use in Linsight | uC & pin type | M A I N | M0+ pin name | SAM uc pin # | SAM pin function | B L A C | 64 M1 # | 64 M1 pin | uC specifics | NI V&V pin type | NI pin name | NI pin # | back- ground data gather | Complicated signal?
A02 | LT GRN | FSC | IGBT Short Circuit Flag | VCM | MCM | 5V=Good, 0V=310A+ (OEM: For at least 500 ms. IGBT: 10us delay). | y | FSC_uC | pin_IGBTshort | 230,5V,VCM | Same | BLAC:INT | n | - | - | - | y | 16 | PB2 | pin change | DO | P0.3 | 68 | n | n
A03 | BLK/YEL | MAMODE2 | ECM IMA request mode | ECM(OD) | MCM | 0V=Assist, 5V=Regen/Standby. If ELD less than 18A, DCDC disabled during assist & autostop (regardless of PWM on other ECM signals). If ELD exceeds 18A, DCDC enabled | y | MAMODE2_uC | pin_MAMODE2 | 2200,5V,MCM | Same | MAIN:INT | y | PA28 | 53 | EVGEN:EXTINT8 | n | - | - | pin change | DO | PFI13 P2.5 | 91 | n | n
A04 | YEL/RED | MOTSTB | Motor Standby | MCM(OD) | ECM | 5V 20Hz 5-10% PWM. Duty cycle never changes when key ON, but lots of noise when engine running. Heartbeat. No CEL: cut MOTSTB & ENGTRQ, then the MCM & ECM sides shorted together. No CEL if driven by (2.2kHz) ENGTRQ PWM. “Sends IMA Motor info to ECM” | y | MOTSTB_uC | pin_motstbPWM | TBD,5V,ECM | 47Ohm Short to ENGTRQ | - | n | - | - | - | n | - | - | Connected to uC just in case | CLKin | P0.20 | 109 | n | n
A06 | YEL/BLK | PDUFAN | MPI Fan Low Speed | MCM(OD) | Relay | MCM grounds 12V relay coil (136 mA) STA315 collector to ground | add batt fan | PDUFAN_uC | pin_pdufanSlow | - | Combined with PDUFANH | MAIN:DO | y | PA27 | 51 | DIO | n | - | - | static | DI, 5V pullup | P0.18 | 107 | n | n
A07 | WHT | PDUFANH | MPI Fan High Speed | MCM(OD) | Relay | MCM grounds 12V relay coil (136 mA) STA315 collector to ground | add batt fan | PDUFANH_uC | pin_pdufanFast | - | Combined with PDUFAN | MAIN:DO | y | PA27 | 51 | DIO | n | - | - | static | DI, 5V pullup | P0.19 | 108 | n | n
A08 | GRY/RED | PRE | Charges IMA caps, then disconnects | MCM | Relay | MCM drives 12V to relay coil (500 mA) via 5151S (IC24) | y | PRE_uC | pin_HVchargeRelay | - | Same | MAIN:DO | y | PB03 | 64 | DIO | n | - | - | static | AI | AI0 | 1 | n | n
A09 | BLK/YEL | IG1 | 12V (ON/Start) | - | - | - | y | KEY_ON_uC | pin_keyon | - | Is car on? | MAIN:INT | y | PB11 | 24 | EVGEN:EXTINT11 | n | - | - | pin change | DI | P0.25 | 115 | n | n
A10 | BLK | PG1 | GND: Near Seats | - | - | MCM shorts to PG2. No other path to LG1/LG2/SG9/SG8/SG4/SG1/SG10. Unpopulated 0603 in MCM would short to LG2. | y | - | - | - | Not used | - | n | - | - | - | n | - | - | - | - | - | - | n | ?
A11 | PNK/BLU | IGA1 | 12V (ON/Start+10s) | - | - | - | y | - | - | - | Not used | - | n | - | - | - | n | - | - | - | - | - | - | n | ?
A13 | GRN/WHT | FOT | IGBT Over Temp Fail Flag | VCM | MCM | 5V=Good, 0V=Overtemp (OEM: at least 2 seconds) |  | FOT_uC | pin_IGBTovertemp | 230,5V,VCM | Same | BLAC:INT | n | - | - | - | y | 23 | PB3 | pin change | DO | PFI12 P2.4 | 89 | n | y
A14 | LTGRN/RED | ABSBUSY | ABS Active Flag | ABS System | MCM | 0V=Good, 5V=ABS active (disables IMA to prevent skidding). Only disables regen (not assist) |  | ABSBUSY_uC | pin_ABSactive | 8300,GND,MCM 3.9k series resistor inside MCM | Same | BLAC:INT | n | - | - | - | y | 24 | PB4 | pin change | DO | PFI11 P2.3 | 87 | n | y
A15 | BLU/WHT | MOTFSB | Motor Assist Failsafe B | MCM(OD) | ECM | 5V Repeating 10 bit data sequence, representing IMA status to ECM (and thus CEL codes). Only four packet types on functonal IMA. Clocked by MOTFSA | y | MOTFSB_uC | pin_MOTFSB_DAT | TBD,5V,ECM | Same | MAIN:UART | y | PA16 | 35 | SERCOM1PAD0 | n | - | - |  | DI | P0.24 | 113 | n | 64M1
A16 | BLU/RED | MOTFSA | Motor Assist Failsafe A | MCM(OD) | ECM | 5V 24Hz 50% clock for MOTFSB. Error if absent 5 seconds. | y | MOTFSA_24HZ_uC | pin_MOTFSA_CLK | TBD,5V,ECM | Same | MAIN:UART | y | PA17 | 36 | SERCOM1PAD1 | n | - | - |  | DI | P0.23 | 112 | n | 64M1
A18 | RED/WHT | WARN | Illuminates 'IMA' Light | MCM(OD) | ECM | Pulling low turns IMA light on. Light pulled to 12V | y | WARN_uC | pin_IMAlight | - | Same | MAIN:DO | y | PA07 | 16 | DIO | n | - | - | static | DI, 5V pullup | P0.4 | 69 | n | 64M1
A21 | BLU/BLK | CNT | Connects Pack HV | MCM | Relay | MCM Drives 12V to relay coil via 5151S (IC25) | y | CNT_uC | pin_HVconnectRelay | - | Same | MAIN:DO | y | PA00 | 1 | DIO | n | - | - | static | AI | AI1 | 4 | n | n
A23 | BLK | PG2 | GND: Near Seats | - | - | - | y | - | - | - | Not used | - | n | - | - | - | n | - | - | - | - | - | - | n | n
A24 | BRN/YEL | LG1 | GND: Engine | - | - | Logic Ground (LG1/LG2/SG9/SG8/SG4/SG1/SG10 shorted in MCM). MCM has no internal path to chassis ground (PG1/PG2)(shorted externally via engine wire harness). | y | GND_ENG | - | - | Same | - | n | - | - |  | n | - | - | - | GND | DGND | 128 | n | n
A25 | BRN | SCS | OBDII Blink Code Enable | DLC | MCM | Pull low to enable blink codes. Pulled to 5V. Never goes low otherwise. | y | SCS_uC | pin_blinkcodes | TBD,5V,TBD | Same | MAIN:INT | y | PB31 | 60 | EVGEN:EXTINT15 | n | - | - | pin change | DO | PFI10 P2.2 | 85 | n | 64M1
A27 | GRN/BLK | DVINH | Enable DC-DC | MCM(OD) | DCDC | 5V=Enable DCDC; 0V=Disable DCDC. Disabled while starting. No CEL if cut. Simple logic (i.e. no PWM). Note: Only the MCM can completely disable the DCDC (via this wire). | y | DVINH_uC | pin_MCMenDCDC | TBD,5V,DCDC | Same | MAIN:DO | y | PB06 | 9 | DIO | n | - | - | static | DI, 5V pullup | P0.5 | 70 | n | 64M1
B01 | PNK/BLU | IGA2 | 12V (ON/Start+10s) | - | - | - | y | - | - | - | Not used | - | n | - | - | - | n | - | - | - | - | - | - | n | n
B02 | YEL/BLK | IGHLD | Powers IMA for ~10s after key off | MCM | IMA Diode | MCM drives 12V to IMA diode via 5151S (IC26) | y | IGHLD_uC | pin_IGHLDrelay | - | Same | MAIN:DO | y | PB23 | 50 | DIO | n | - | - | static | AI | AI2 | 7 | n | n
B06 | GRN | IWPH | Measures Phase W Current | W I Sensor | MCM | 0:5V sinusoid. Assist below 2.5 VDC. ~8mV/A nominally from 2.5 V. DO NOT LOAD!! | y | W_CURRENT_uC | pin_Wcurrent | - | Same | BLAC:ADC | n | - | - | - | y | 17 | PC4 | analog | AO | AO1 | 31 | n | n
B07 | RED/BLU | IVPH | Measures Phase V Current | V I Sensor | MCM | 0:5V sinusoid. Assist below 2.5 VDC. ~8mV/A nominally from 2.5 V. DO NOT LOAD!! | y | V_CURRENT_uC | pin_Vcurrent | - | Same | BLAC:ADC | n | - | - | - | y | 18 | PC5 | analog | AO | AO1 | 31 | n | 64M1
B08 | WHT | IUPH | Measures Phase U Current | U I Sensor | MCM | 0:5V sinusoid. Assist below 2.5 VDC. ~8mV/A nominally from 2.5 V. DO NOT LOAD!! | y | U_CURRENT_uC | pin_Ucurrent | - | Same | BLAC:ADC | n | - | - | - | y | 26 | PB5 | analog | AO | AO1 | 31 | n | 64M1
B09 | BRN/YEL | LG2 | GND: Engine | - | - | - | y | GND_ENG | - | - | Same | - | y | - | 22,33,47,54 | GND | n | - | - | - | - | - | - | n | 64M1
B10 | WHT/RED | VBU | 12V (Always) | - | - | This line has 550 mOhm round trip ESR (via LG2) | y | - | - | - | Main Power | - | n | - | - | - | n | - | - | - | AI | AI3 | 10 | n | 64M1
B13 | YEL/BLU | TDV | DC-DC Temp | DCDC | MCM | Analog temperature 2.663 VDC @ ~70degF | y | TDV_uC | pin_ADCtempDCDC | 5400,5V,MCM | Same | MAIN:AI | y | PB05 | 6 | ADC1:MUXPOS:AIN7 | n | - | - | average | AO | AO2 | 47 | ADC | 64M1
B14 | BLU/RED | TD | IGBT Temp | VCM | MCM | OEM: 2.700 VDC @ ~70degF. Linsight:21.67kOhm pullup to 4.918V yields 2.460V @ ~70degF | y | TD_uC | pin_ADCtempIGBT | 20000,5V,MCM | Same | MAIN:AI | y | PB00 | 61 | ADC1:MUXPOS:AIN0 | n | - | - | average | AO | AO2 | 47 | ADC | 64M1
B16 | ORG | VPIN | IMA Batt voltage | VCM | MCM | VPIN=Vbatt/[51.0:52.6] (0:5VDC opamp output) 100kUP&DN. Nonlinear at lower voltage (e.g. only 30x@31.5V). ESR=225 Ohms (114mV drop with 505uA load) | remove vdiv | VPIN_uC | pin_ADCvoltageIGBT | - | Vmeas=Vbatt/69. | MAIN:AI | y | PB01 | 62 | ADC1:MUXPOS:AIN1 | n | - | - | average | AO | AO3 | 63 | ADC | 64M1
B18 | YEL/BLK | IPIN | Measured IMA motor current from battery | MPI I Sensor | MCM | 0:5VDC output, 10mV/A |  | BATT_I_SENSE_uC | pin_ADCbattIsense | - | Ibattery | MAIN:AI | y | PA04 | 13 | ADC0:MUXPOS:AIN4 | n | - | - | accumulate | AI | AI4 | 17 | n | n
B19 | RED/BLK | SG9 | GND: VPIN Reference | - | - | shorted to GNDENG in MCM, but not in IGBT predriver | y | - | - | - | GNDA(ILTC to GND) | - | n | - | - | - | n | - | - | - | - | - | - | n | n
B21 | BRN | SG8 | GND: MPI W Sensor | - | - | Connects only to sensor | y | - | - | - | OD GND | - | n | - | - | - | n | - | - | - | - | - | - | n | n
B22 | GRY | SG7 | GND: MPI V Sensor | - | - | Connects only to sensor | y | - | - | - | OD GND | - | n | - | - | - | n | - | - | - | - | - | - | n | y
B23 | BLU/ORG | SG6 | GND: MPI U Sensor | - | - | Connects only to sensor | y | - | - | - | OD GND | - | n | - | - | - | n | - | - | - | - | - | - | n | y
B25 | RED/YEL | SG4 | GND: MPI Current Sensor | - | - | - | y | - | - | - | Same | - | n | - | - | - | n | - | - | accumulate | AO | AO0 | 15 | ADC | n
C01 | BLU/YEL | ENGTRQ | Engine Torque | ECM(OD) | MCM | 5V 2.2kHz 10% PWM. Never changes. CEL&IMA if wire is cut (P1647[03]), unless 10% PWM placed on MCM side of cut. ECM side can remain floating (it's OD). No CEL if driven@1 kHz. No CEL if MOTSTB & ENGTRQ cut and then the MCM and ECM sides shorted together | y | ENGTRQ_uC | pin_engtrq | TBD,5V,MCM | 47Ohm Short to MOTSTB | - | n | - | - | - | n | - | - | Connected to uC just in case | PWMout | PFI5 P1.5 | 78 | n | n
C02 | BLU/BLK | CMDPWR | 2kHz PWM (Regen<50%, Assist>50%) | ECM(OD) | MCM | 5V 2kHz PWM (10:90%). Pulled high when 'OFF' until HV disconnects | y | CMDPWR_uC | pin_cmdpwr | TBD,5V,MCM | Same | MAIN:PWMin | y | PB02 | 63 | TC2/WO0 | n | - | - |  | PWMout | PFI6 P1.6 | 79 | PWM | y
C04 | BLU/WHT | VSS | Wheel Speed | VSS | MCM | 5V Pulses each time the speedometer gear rotates. ~4000 pulses/mile (89 Hz@80mph) | y | VSS_uC | pin_WheelPulse | TBD,5V,VSS | Same | MAIN:CNTin | y | PA10 | 19 | TCC1/WO0 or FREQm (via GCLK_IO4) | n | - | - |  | CTRout | PFI3 P1.3 | 76 | counter | n
C05 | YEL/BLK | ACTTRQ | Actual IMA Torque Delivered | MCM(OD) | ECM | 5V 2kHz PWM. 50%=0 torque. assist above 50%. 50% while starting. No CEL if 50%duty at 20Hz (i.e. by MOTFSA clockl) | y | ACTTRQ_uC | pin_acttrqPWM | TBD,5V,ECM | Same | MAIN:PWMout | y | PA18 | 37 | TC4/WO0 | n | - | - |  | CNTin | P0.21 | 110 | n | n
C06 | LTGRN/RED | UL | Phase U Low side IGBT | MCM | VCM | MCM drives PNP base (emitter=5V, collector drives IGBTpredriver through 220 Ohm Rseries). |  | UL_uC | pin_UL | 3880,LG1,VCM | Same | BLAC:PWM | n | - | - | - | y | 28 | PB7 | PSC | DI | P0.6 | 71 | n | n
C07 | BLU/BLK | UH | Phase U High Side IGBT | MCM | VCM | Idle: 0:5V square PWM chopped@8kHz. |  | UH_uC | pin_UH | 3880,LG1,VCM | Same | BLAC:PWM | n | - | - | - | y | 29 | PD0 | PSC | DI | P0.7 | 72 | n | n
C09 | BLU/ORG | METSCI2 | SoC+Assist/Regen to Gauge & BCM 'B' | MCM | BCM & Gauge | 5V. data every 100ms. Diff pair | y | UART_METSCI_RX | pin_METSCIrx | - | Gauge (only) | MAIN:UART | y | PB15 | 28 | SERCOM4PAD3 | n | - | - |  | DI | P0.8 | 97 | n | y
C10 | WHT/BLU | METSCI1 | SoC+Assist/Regen to Gauge & BCM 'A' | MCM | BCM & Gauge | 5V. data every 100ms. Diff pair | y | UART_METSCI_TX | pin_METSCItx | - | Gauge (only) | MAIN:UART | y | PB08 | 11 | SERCOM4PAD0 | n | - | - |  | DI | P0.9 | 98 | Serial | y
C12 | RED/YEL | MAMODE1 | ECU Requested IMA Mode | ECM(OD) | MCM | 5V 20.04kHz PWM: Asst@25%;Regen@35%;Start@85%;Standby@50%;Prestart@15%;AutoStop@70% | y | MAMODE1_uC | pin_IMAmodeRequest | TBD,5V,MCM | Same | MAIN:PWMin | y | PB12 | 25 | TC0/WO0 | n | - | - |  | PWMout | PFI7 P1.7 | 80 | PWM | n
C14 | BLU | NEP | Tachometer pulses | ECM | MCM | 12V 50% duty. 1 pulse/engRevolution (44.1 ms period@idle) 100Hz@6krpm, 33Hz@2krpm | y | NEP_uC | pin_TachPulse | TBD,12V,ECM | Same | MAIN:CNTin | y | PB30 | 59 | TCC0/WO0 | n | - | - |  | CTRout | PFI4 P1.4 | 77 | counter | n
C16 | PNK | QBATT | Battery SOC | MCM(OD) | ECM | 5V 2kHz PWM. Duty cycle is how charged the ECM thinks the IMA battery is. 10%=empty, 90%=full. The ECM will force charge the battery with 10% duty, no matter how full the battery actually is. No CEL if driven by (2.2kHz) ENGTRQ PWM. | y | QBATT_uC | pin_BattSOC | TBD,5V,ECM | Same | MAIN:PWMout | y | PA19 | 38 | TC4/WO1 | n | - | - |  | CNTin | P0.22 | 111 | n | n
C17 | YEL/RED | VL | Phase V Low side IGBT | MCM | VCM | MCM only drives line to Vcc or leaves it floating (pulldown in IGBTpredriver pulls low) |  | VL_uC | pin_VL | 3880,LG1,VCM | Same | BLAC:PWM | n | - | - | - | y | 27 | PB6 | PSC | DI | P0.10 | 99 | n | n
C18 | BLK/ORG | VH | Phase V High Side IGBT | MCM | VCM | IGBT driver is 22 kW max continuous (541 W max total sunk in IGBTs). |  | VH_uC | pin_VH | 3880,LG1,VCM | Same | BLAC:PWM | n | - | - | - | y | 30 | PC0 | PSC | DI | P0.11 | 100 | n | n
C20 | LT BLU | TDX/RDX | OBDII Diagnostic Bus (“H-Line”) | DLC/MCM | MCM/DLC | Startup behavior: see video. No other activity observed unless OBDII tool plugged in. Idle:5V. Connects to ABS/EPS/SRS | y | UART_H-LINE | pin_Hline | 4700,5V,MCM | Same | MAIN:UART | y | PA12 | 29 | SERCOM2PAD0 | n | - | - | - | DI | P0.12 | 101 | Serial | n
C21 | WHT | BATTSCI2 | BCM->MCM Serial 'B' | BCM | MCM | Sends battery data to MCM. Diff bus. Not used in Linsight | y | - | - | - | Not used | - | n | - | - | - | n | - | - | - | - | - | - | n | n
C22 | ORG | BATTSCI1 | BCM->MCM Serial 'A' | BCM | MCM | Sends battery data to MCM. Diff bus. Not used in Linsight | y | - | - | - | Not used | - | n | - | - | - | n | - | - | - | - | - | - | n | n
C24 | GRN/WHT | VCC7 | 5V: MPI Current Sensor | - | - | - | y | - | - | - | Same | - | n | - | - | - | n | - | - | - | - | - | - | n | n
C25 | YEL | VCC6 | 5V: MPI W Sensor | - | - | All 5V derived from 12V LDO: 3003S (IC23) | y | - | - | - | Same | - | n | - | - | - | n | - | - | - | - | - | - | n | n
C26 | YEL/BLU | VCC5 | 5V: MPI V Sensor | - | - | - | y | - | - | - | Same | - | n | - | - | - | n | - | - | - | - | - | - | n | n
C27 | GRY/RED | WL | Phase W Low side IGBT | MCM | VCM | IGBT manual recommends at least 2.5 us dead time and PWM frequency less than 20kHz. That's 125 clock cycles@50MHz |  | WL_uC | pin_WL | 3880,LG1,VCM | Same | BLAC:PWM | n | - | - | - | y | 9 | PB1 | PSC | DI | P0.13 | 102 | n | n
C28 | BLK/YEL | WH | Phase W High Side IGBT | MCM | VCM | IGBT sinks 175 W @ 100 A drive. |  | WH_uC | pin_WH | 3880,LG1,VCM | Same | BLAC:PWM | n | - | - | - | y | 8 | PB0 | PSC | DI | P0.14 | 103 | n | n
C29 | GRN/BLK | VCC4 | 5V: MPI U Sensor | - | - | - | y | - | - | - | Same | - | n | - | - | - | n | - | - | - | - | - | - | n | n
D01 | BLK | VCC1 | 5V: A Hall Sensor | - | - | - | y | - | - | - | Same | - | n | - | - | - | n | - | - | - | - | - | - | n | y
D02 | WHT | CMA | Motor Sensor A Position | A Hall Sensor | MCM | 6 electrical periods per mechanical revolution. Electrically in phase with Phase W |  | H1_uC | pin_hall_1 | 2200,5V,MCM | Same | BLAC:INT | n | - | - | - | y | 32 | PD1 | PSC | DO | P0.0 | 65 | n | y
D04 | RED | SG1 | GND: A Hall Sensor | - | - | - | y | - | - | - | OD GND | - | n | - | - | - | n | - | - | - | - | - | - | n | y
D05 | BLU/WHT | SG10 | GND: DCDC & VCM | - | - | Shorted to LG1/2 inside MCM, but not inside VCM | y | - | - | - | Same | - | n | - | - | - | n | - | - | - | - | - | - | n | n
D06 | YEL | VCC2 | 5V: B Hall Sensor | - | - | - | y | - | - | - | Same | - | n | - | - | - | n | - | - | - | AI | AI6 | 23 | n | n
D08 | GRN | CMB | Motor Sensor B Position | B Hall Sensor | MCM | 5V 50% square wave. 9ms period@1dle~=1krpm. Electrically in phase with Phase V |  | 'H3_uC' | MAIN: pin_BLAC_MISO_BitBang BLAC: pin_hall_3 | 2200,5V,MCM | BLAChall MAINprogramming | BOTH: MAIN:DI BLAC:INT | y | PB09 | 12 | DIO | y | 1 | PD2 | PSC(BLAC) | DO | P0.2 | 67 | n | n
D10 | BLU | SG2 | GND: B Hall Sensor | - | - | - | y | - | - | - | OD GND | - | n | - | - | - | n | - | - | - | - | - | - | n | n
D13 | GRN/BLU | VCC3 | 5V: C Hall Sensor | - | - | - | y | - | - | - | Same | - | n | - | - | - | n | - | - | - | - | - | - | n | n
D14 | RED | VREF | 5V: VPIN Reference | - | - | Supplies lowpassed 5V signal to VPIN. | y | - | - | - | Same | - | n | - | - | - | n | - | - | - | AI | AI7 | 26 | n | n
D15 | BRN | CMC | Motor Sensor C Position | C Hall Sensor | MCM | Electrically in phase with Phase U Valid state patterns (ABC): LLH→HLH→HLL→HHL→LHL→LHH→LLH, or; LLH→LHH→LHL→HHL→HLL→HLH→LLH (above, backwards) CMA is: 20 deg before CMB, and: 40 deg before CMC |  | H2_uC | pin_hall_2 | 2200,5V,MCM | Same | BLAC:INT | n | - | - | - | y | 3 | PC1 | PSC | DO | P0.1 | 66 | n | n
D16 | WHT | SG3 | GND: C Hall Sensor | - | - | - | y | - | - | - | OD GND | - | n | - | - | - | n | - | - | - | AI | AI5 | 20 | n | n
E04 | WHT | VHB- | Negative Stack Voltage | IMA Battery | MCM | Not used in Linsight | y | - | - | - | - | - | n | - | - | - | n | - | - | - | - | - | - | n | y
E08 | RED | VHB+ | Positive Stack Voltage | IMA Battery | MCM | Not used in Linsight | y | - | - | - | - | - | n | - | - | - | n | - | - | - | - | - | - | n | y
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

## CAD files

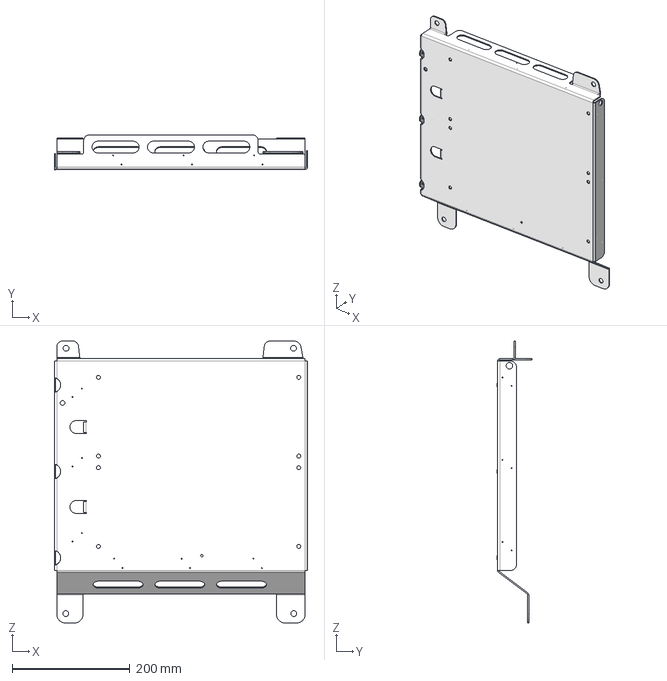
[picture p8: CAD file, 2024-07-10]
Mechanicals/47 Ah FoMoCo Tray/RevB/LiBCM003 - Battery Tray/LiBCM003 - Lower Tray - RevB.stp
431.1 x 60.3 x 479.9 mm

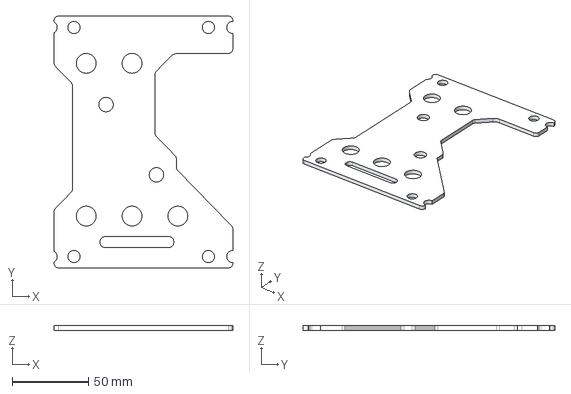
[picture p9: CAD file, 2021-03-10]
Mechanicals/Battery End Plate/V4/LiBCM End Plate - RevA.stp
117.0 x 165.0 x 3.17 mm

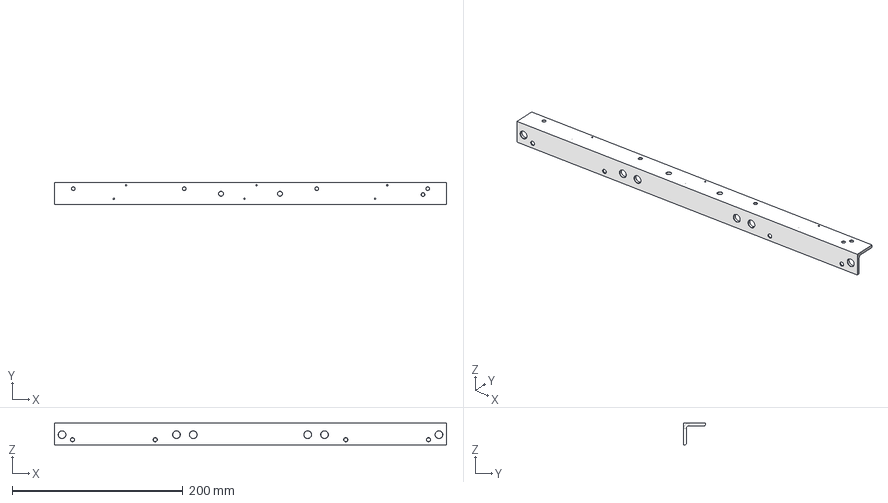
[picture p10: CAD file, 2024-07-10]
Mechanicals/47 Ah FoMoCo Tray/RevB/LiBCM004 - Battery Rail/LiBCM004 - Battery Rail - RevA.stp
459.3 x 25.4 x 25.4 mm

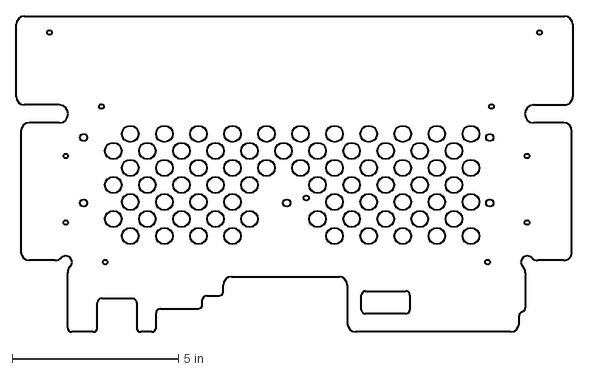
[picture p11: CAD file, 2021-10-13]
Mechanicals/Safety Cover/LiBCM Safety Cover - RevC/Safety Cover - RevC_FLAT.dxf
16.7 x 9.49 in

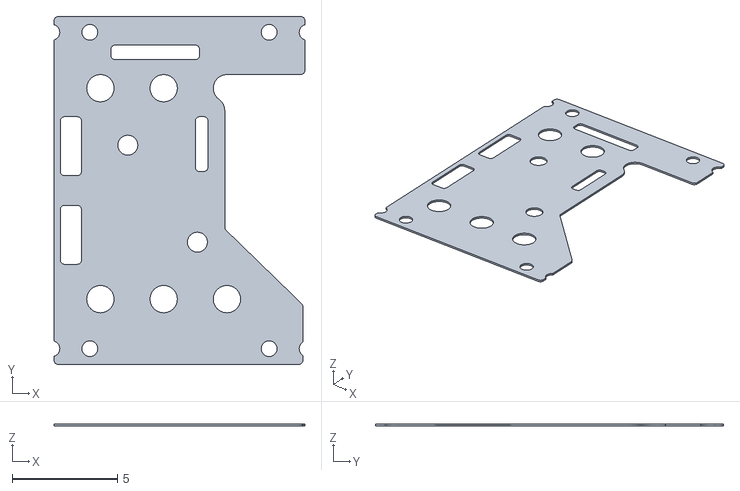
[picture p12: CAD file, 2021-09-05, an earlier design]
Mechanicals/Battery End Plate/V2/End Plate - 18S.stl
11.9 x 16.5 x 0.1

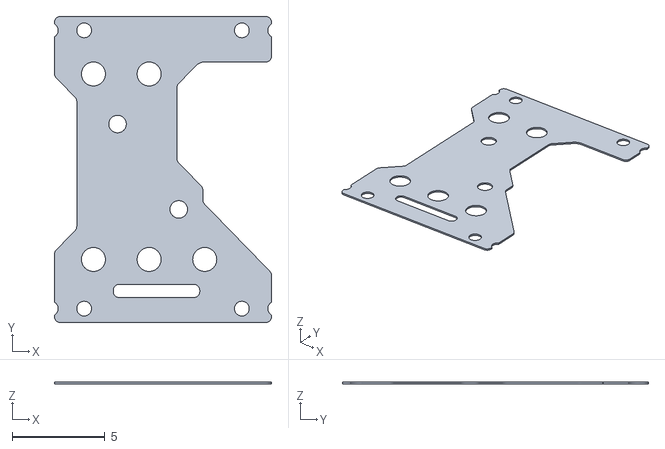
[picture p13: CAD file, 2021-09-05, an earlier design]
Mechanicals/Battery End Plate/V3/End Plate - 18S.stl
11.7 x 16.5 x 0.1

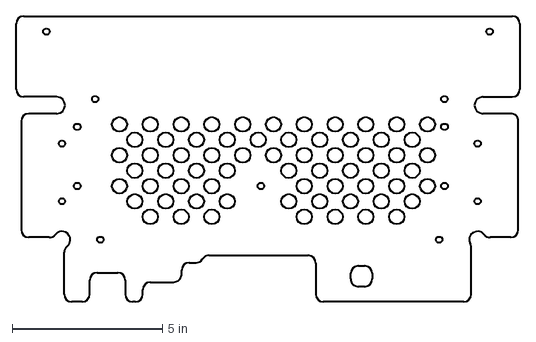
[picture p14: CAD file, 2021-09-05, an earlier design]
Mechanicals/Safety Cover/LiBCM Safety Cover - RevA/Safety Cover.dxf
16.7 x 9.50 in

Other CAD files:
Mechanicals/47 Ah FoMoCo Tray/RevB/Battery Modules/47Ah-FoMoCo.dwg
Mechanicals/47 Ah FoMoCo Tray/RevB/LiBCM004 - Battery Rail/Bracket - 5th Module 8982K875.dwg
Mechanicals/47 Ah FoMoCo Tray/RevB/LiBCM005 - Charger Mount/Charger Mount.dwg
Mechanicals/Cable Construction/HVDC 4AWG Cables/Cable Primitive.dwg
Mechanicals/Honda G3 Lithium Batteries/Cell.dwg
Mechanicals/Safety Cover/LiBCM Safety Cover - RevC/Safety Cover.dwg
Mechanicals/47 Ah FoMoCo Tray/RevB/LiBCM003 - Battery Tray/47 Ah FoMoCo Aluminum Tray.dwg
Mechanicals/47 Ah FoMoCo Tray/RevA/LiBCM003 - Battery Tray/47 Ah FoMoCo Aluminum Tray.dwg
Mechanicals/47 Ah FoMoCo Tray/RevA/LiBCM004 - Battery Rail/Bracket - 5th Module 8982K875.dwg
Mechanicals/47 Ah FoMoCo Tray/RevA/LiBCM005 - Charger Mount/Charger Mount.dwg
Mechanicals/Safety Cover/LiBCM Safety Cover - RevB/Safety Cover - Glowforge 20x12.dwg
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

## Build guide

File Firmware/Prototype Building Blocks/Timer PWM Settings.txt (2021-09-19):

MEGA2560

You can double the frequency on any counter by switching to fast PWM. Example:
TCCR2A = (TCCR2A & 0b11111100) | 0b00000011; // set WGM00, WGM01 to 1: xxxxxx11 for fast PWM

You can set any frequency you want by configuring a timer's compare registers

...

//never mess with this one as it directly affects delay and millis
//---------------------------------------------- Set PWM frequency for D4 & D13 --------------------------
//TCCR0B = TCCR0B & B11111000 | B00000001; // set timer 0 divisor t     1 for PWM frequency of 62500.00 Hz
//TCCR0B = TCCR0B & B11111000 | B00000010; // set timer 0 divisor to    8 for PWM frequency of  7812.50 Hz
//TCCR0B = TCCR0B & B11111000 | B00000011; // set timer 0 divisor to   64 for PWM frequency of   976.56 Hz (Default)
//TCCR0B = TCCR0B & B11111000 | B00000100; // set timer 0 divisor to  256 for PWM frequency of   244.14 Hz
//TCCR0B = TCCR0B & B11111000 | B00000101; // set timer 0 divisor to 1024 for PWM frequency of    61.04 Hz

//---------------------------------------------- Set PWM frequency for D11 & D12 --------------------------
//TCCR1B = TCCR1B & B11111000 | B00000001; // set timer 1 divisor to     1 for PWM frequency of 31372.55 Hz
//TCCR1B = TCCR1B & B11111000 | B00000010; // set timer 1 divisor to     8 for PWM frequency of  3921.16 Hz
//TCCR1B = TCCR1B & B11111000 | B00000011; // set timer 1 divisor to    64 for PWM frequency of   490.20 Hz (Default)
//TCCR1B = TCCR1B & B11111000 | B00000100; // set timer 1 divisor to   256 for PWM frequency of   122.55 Hz
//TCCR1B = TCCR1B & B11111000 | B00000101; // set timer 1 divisor to  1024 for PWM frequency of    30.64 Hz

//---------------------------------------------- Set PWM frequency for D9 & D10 ---------------------------
//TCCR2B = TCCR2B & B11111000 | B00000001; // set timer 2 divisor to     1 for PWM frequency of 31372.55 Hz
//TCCR2B = TCCR2B & B11111000 | B00000010; // set timer 2 divisor to     8 for PWM frequency of  3921.16 Hz
//TCCR2B = TCCR2B & B11111000 | B00000011; // set timer 2 divisor to    32 for PWM frequency of   980.39 Hz
//TCCR2B = TCCR2B & B11111000 | B00000100; // set timer 2 divisor to    64 for PWM frequency of   490.20 Hz (Default)
//TCCR2B = TCCR2B & B11111000 | B00000101; // set timer 2 divisor to   128 for PWM frequency of   245.10 Hz
//TCCR2B = TCCR2B & B11111000 | B00000110; // set timer 2 divisor to   256 for PWM frequency of   122.55 Hz
//TCCR2B = TCCR2B & B11111000 | B00000111; // set timer 2 divisor to  1024 for PWM frequency of    30.64 Hz

//---------------------------------------------- Set PWM frequency for D2, D3 & D5 ------------------------
//TCCR3B = TCCR3B & B11111000 | B00000001; // set timer 3 divisor to     1 for PWM frequency of 31372.55 Hz
//TCCR3B = TCCR3B & B11111000 | B00000010; // set timer 3 divisor to     8 for PWM frequency of  3921.16 Hz
//TCCR3B = TCCR3B & B11111000 | B00000011; // set timer 3 divisor to    64 for PWM frequency of   490.20 Hz (Default)
//TCCR3B = TCCR3B & B11111000 | B00000100; // set timer 3 divisor to   256 for PWM frequency of   122.55 Hz
//TCCR3B = TCCR3B & B11111000 | B00000101; // set timer 3 divisor to  1024 for PWM frequency of    30.64 Hz

//---------------------------------------------- Set PWM frequency for D6, D7 & D8 ------------------------
//TCCR4B = TCCR4B & B11111000 | B00000001; // set timer 4 divisor to     1 for PWM frequency of 31372.55 Hz
//TCCR4B = TCCR4B & B11111000 | B00000010; // set timer 4 divisor to     8 for PWM frequency of  3921.16 Hz
//TCCR4B = TCCR4B & B11111000 | B00000011; // set timer 4 divisor to    64 for PWM frequency of   490.20 Hz (Default)
//TCCR4B = TCCR4B & B11111000 | B00000100; // set timer 4 divisor to   256 for PWM frequency of   122.55 Hz
//TCCR4B = TCCR4B & B11111000 | B00000101; // set timer 4 divisor to  1024 for PWM frequency of    30.64 Hz

//---------------------------------------------- Set PWM frequency for D44, D45 & D46 ---------------------
//TCCR5B = TCCR5B & B11111000 | B00000001; // set timer 4 divisor to     1 for PWM frequency of 31372.55 Hz
//TCCR5B = TCCR5B & B11111000 | B00000010; // set timer 4 divisor to     8 for PWM frequency of  3921.16 Hz
//TCCR5B = TCCR5B & B11111000 | B00000011; // set timer 4 divisor to    64 for PWM frequency of   490.20 Hz (Default)
//TCCR5B = TCCR5B & B11111000 | B00000100; // set timer 4 divisor to   256 for PWM frequency of   122.55 Hz
//TCCR5B = TCCR5B & B11111000 | B00000101; // set timer 4 divisor to  1024 for PWM frequency of    30.64 Hz

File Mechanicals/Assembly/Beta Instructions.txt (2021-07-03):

Remove the OEM battery from the IMA bay.

Remove the NiMH sticks from the battery enclosure.

Let's look at the OEM parts you're going to need to use LiBCM:
Step 0:
https://youtu.be/0KqhpafInwc

Next let's look at the LiBCM kit.  With any luck, I've sent all the parts shown in this video:
Step 1:
https://youtu.be/b1Am878clMo

The first step is to modify the OEM MCM'E' & temperature cables for use with LiBCM.  This video editing is really bad... I made a technical mistake at some point and didn't realize until much later... in my attempt to edit a cohesive video together, I've created a linearly, technically correct list of steps, but it's a bit choppy aesthetically:
LiBCM Beta - Step 2: MCM'E' & Temp Cable Prep
https://youtu.be/WAM3-0bZgP8

...

The audio volume is quiet in the next few videos... I was filming this video at 4AM, with my wife sleeping in the next room over... also, the microphone wasn't placed well.  Again, I'll be re-recording the entire installation process with better equipment and a wireless microphone for general release.

LiBCM Beta - Step 3: Junction Board and Battery Case Modifications
https://youtu.be/3Lgjrowf5Xw

...

Next let's install the batteries.  Remember you're dealing with high voltage.  Don't touch more than one thing at a time!
LiBCM Beta - Step 4: Installing Batteries
https://youtu.be/lDXR1nHAS50

...

Next we'll install the PCB and the various wires that plug into it:
LiBCM Beta - Step 5
https://youtu.be/YIbVGhcSc5o

...

Now let's throw the complete pack into the IMA bay, load the firmware, and talk through a beta quirk (that will go away with better firmware):
LiBCM Beta - Step 6
https://youtu.be/IHuEETffAaQ
The MVP firmware I mentioned in this video is here:
https://github.com/doppelhub/Honda_Insight_LiBCM/MVP/MVP.ino

If you are using the "+40% current hack", then no code changes are required.
If you are using the OEM current settings, then comment out line 172 (as of this writing) in MVP.ino.  Specifically, add '//' to the beginning of line 172:
//battCurrent_amps = (int16_t)(battCurrent_amps * 0.7);

...

Finally, here's how to route the wires in the middle mat area:
LiBCM Beta - Step 7
https://youtu.be/T0TkoDq_NlQ

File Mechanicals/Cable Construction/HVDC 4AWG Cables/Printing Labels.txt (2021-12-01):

Printing labels:
-Use "chain print" feed option
-Add 15 spaces between each "BAY2+" label

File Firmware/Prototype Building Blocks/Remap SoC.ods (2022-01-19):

LiBCM SoC (percent) | MCM SoC (decipercent)
0 | 0
1 | 22
2 | 44
3 | 67
4 | 89
5 | 111
6 | 133
7 | 156
8 | 178
9 | 190
10 | 200 | get to 20% here
11 | 209
12 | 217
13 | 225
14 | 232
15 | 240
16 | 248
17 | 256
18 | 264
19 | 272
20 | 279
21 | 287
22 | 295
23 | 303
24 | 311
25 | 319
26 | 326
27 | 334
28 | 342
29 | 350
30 | 355
31 | 363
32 | 375
33 | 387
34 | 399
35 | 411
36 | 423
37 | 435
38 | 447
39 | 459
40 | 471
41 | 483
42 | 495
43 | 507
44 | 519
45 | 532
46 | 544
47 | 556
48 | 568
49 | 580
50 | 592
51 | 604
52 | 616
53 | 628
54 | 640
55 | 652
56 | 664
57 | 676
58 | 688
59 | 700
60 | 701 |  |  | Low range
61 | 705 |  |  |  | low | high
62 | 709 |  |  | input | 86 | 100
63 | 713 |  |  | output | 800 | 1000
64 | 717
65 | 721
66 | 725
67 | 728
68 | 732
69 | 736
70 | 740
71 | 744
72 | 748
73 | 752
74 | 756
75 | 760
76 | 764
77 | 768
78 | 772
79 | 775
80 | 779
81 | 783
82 | 787 |  | regen disabled at 80%
83 | 791
84 | 795
85 | 799
86 | 800
87 | 814
88 | 829
89 | 843
90 | 857
91 | 871
92 | 886
93 | 900
94 | 914
95 | 929
96 | 943
97 | 957
98 | 971
99 | 986
100 | 1000

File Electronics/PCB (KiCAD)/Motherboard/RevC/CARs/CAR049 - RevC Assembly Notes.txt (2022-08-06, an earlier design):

RevC Assembly Notes:
R130 should be 1206
R353 silkscreen
Move middle (rear) temp connector so it doesn't hit ribbon cable's locking tab
Move beeper and Cherry switch up ~1mm
Silkscreen text overlaps near (right of) C95.

/////////////////////////////////////////////////////////////////////////////////

Solution:
R130 changed to 1206
Fixed silkscreen issues
Didn't move temp connector, beeper, or cherry switch

Done

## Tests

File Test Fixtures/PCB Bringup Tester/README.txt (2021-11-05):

To Use:
1: Rename "MVP.ino" -> "MVP.MASTER" (so Arduino ignores it).
2: Rename "BringupTester.txt" -> "BringupTester.ino.
3: Rename main "MVP" folder -> "BringupTester" (to make Arduino happy).
4: Build Firmware.

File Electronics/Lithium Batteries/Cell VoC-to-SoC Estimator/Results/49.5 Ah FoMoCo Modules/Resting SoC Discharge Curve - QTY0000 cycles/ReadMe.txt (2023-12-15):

Starting condition:
Single 49.5 Ah cell charged to 4.15 volts at 5.5 amps.

Test:
Cell continuously discharged at 3.0 amps (C/16.5) down to 2.8 volts.
Cell voltage measured every second (the test data).

The results from this data are used to calculate SoC from resting Voc.

Note:
The raw data has several "0.00" volt readings, which occur when the received checksum doesn't match.  This data can be discarded.  There are way more data points than are required to draw useful conclusions.

I should rewrite the code to make it prevent writing errant data... but I'm not going to do that now.  Any non-zero value is accurate. Code is identical to 47Ah (use that code). Couldn't get programmable load to work in macOS, so used old Windows 7 image on 2013MBP.

...

Since the point of this test was to see if the so-called "49.5 Ah" and "47 Ah" Samsung modules were identical, see the 47 Ah test results for a comparative analysis.  In short, both modules are identical.

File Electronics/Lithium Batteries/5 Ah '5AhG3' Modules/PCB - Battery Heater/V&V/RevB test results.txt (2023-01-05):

18S+- (First Test):

19:34:18.868 -> Temperatures:
19:34:18.907 -> BAY1: 12
19:34:18.907 -> BAY2: 14
19:34:18.907 -> BAY3: 14

00:27:25.229 -> Temperatures:
00:27:25.229 -> BAY1: 8
00:27:25.229 -> BAY2: 9
00:27:25.229 -> BAY3: 9

01:19:13.405 -> Temperatures:
01:19:13.405 -> BAY1: 7
01:19:13.405 -> BAY2: 8
01:19:13.405 -> BAY3: 8

06:27:52.200 -> Temperatures:
06:27:52.200 -> BAY1: -4
06:27:52.200 -> BAY2: -2
06:27:52.200 -> BAY3: -2

...

18S-- (2nd Test):

Outside, heaters off:
14:31:34.278 -> Temperatures:
14:31:34.278 -> BAY1: 4
14:31:34.278 -> BAY2: 6
14:31:34.278 -> BAY3: 5

15:04:47.184 -> Temperatures:
15:04:47.184 -> BAY1: 1
15:04:47.184 -> BAY2: 4
15:04:47.184 -> BAY3: 2

15:06: Turned all three supplies on:
12S: 134V@ 95mA = 12.7 W
18S: 134V@142mA = 19.0 W
18S: 134V@15xmA = 19.0 W (using larger lambda gen with lower resolution)

16:29:22.471 -> Temperatures:
16:29:22.471 -> BAY1: 8
16:29:22.471 -> BAY2: 14
16:29:22.471 -> BAY3: 14

17:00:12.899 -> Temperatures:
17:00:12.899 -> BAY1: 9
17:00:12.899 -> BAY2: 17
17:00:12.899 -> BAY3: 16

17:18:36.120 -> Temperatures:
17:18:36.120 -> BAY1: 9
17:18:36.120 -> BAY2: 18
17:18:36.120 -> BAY3: 17

18:27:33.235 -> Temperatures:
18:27:33.235 -> BAY1: 12
18:27:33.235 -> BAY2: 22
18:27:33.235 -> BAY3: 21

19:16:43.270 -> Temperatures:
19:16:43.270 -> BAY1: 13
19:16:43.270 -> BAY2: 23
19:16:43.270 -> BAY3: 22

21:56:14.406 -> Temperatures:
21:56:14.406 -> BAY1: 14
21:56:14.406 -> BAY2: 27 (outside: -12)
21:56:14.406 -> BAY3: 25

Test 2 conclusions:
In 18S-- configuration, both 18S modules have similar temp, and much higher than needed.  For some reason, the 12S module is still lagging far behind.  So we need to increase 12S module power, and also need to decrease 18S module power; there's no reason we need to head pack up to 27 degC when it's -12 outside... that's a 39 degree delta!

So we're going to test the following with 18S--:
-Decrease power in both 18S modules.  Since they're tracking the same, probably decrease them uniformly.
-Increase power in 12S module.
-Retest 18S+- configuration (with better wind shielding).
-I'm going to try setting all three modules to the same power: 17 W

12S ESR (3k9 installed): 1410.5 Ohms
12S V_new: 154.9 volts (17 watts)
Average power into each 12S cell: 1.42 W

18S ESR (3k9 installed): 943.7 Ohms
18S V_new: 126.7 volts 17 watts
Average power into each 18S cell: 0.94 W

Implemented this change at 10:14PM 2022DEC23

...

Test 3: All heater PCBs @ 17 watts (3k9 resistors installed)
The goal of this test is to get the temp sensors in the middle of each module to read the same temperature.  We also need to increase power at each end of all modules, to better balance the temperature gradient.  This will require removing the modules again (which will be test #4).

Test3 started at 10:14PM 2022DEC23, immediately after text2 finished.
Still using 18S-- configuration.

22:23:34.358 -> Temperatures:
22:23:34.358 -> BAY1: 15
22:23:34.358 -> BAY2: 27
22:23:34.358 -> BAY3: 24

22:28:04.323 -> Temperatures:
22:28:04.323 -> BAY1: 15
22:28:04.323 -> BAY2: 27
22:28:04.323 -> BAY3: 25

22:37:58.917 -> Temperatures:
22:37:58.917 -> BAY1: 15
22:37:58.917 -> BAY2: 27
22:37:58.917 -> BAY3: 24

00:56:31.580 -> Temperatures:
00:56:31.580 -> BAY1: 18
00:56:31.580 -> BAY2: 26
00:56:31.580 -> BAY3: 24
00:56:33.066 -> temp:18

After 2.5 hours, 12S only warmed up 3 degC... so 12S needs even more power (relative to 18S).  I'm gonna give 12S 5 more watts:
12S ESR (3k9 installed): 1410.5 Ohms
12S V_new: 176.0 volts (22 watts)
Average power into each 12S cell: 1.83 W

18S ESR (3k9 installed): 943.7 Ohms
18S V_new: 119.0 volts 15 watts
Average power into each 18S cell: 0.83 W

Implemented this change at 10:14PM 2022DEC23

...

Test 4: Each 12S cell is getting +1 watt more than each 18S cell (1.83 vs 0.83 W).  This doesn't make any sense.

Test4 begins immediately after Test3. 18S--.

12S: 176V@126mA = 22.2 W
18S: 119V@126mA = 15.0 W
18S: 119V@13xmA = 15.0 W (using larger lambda gen with lower resolution)

Shortly after starting Test4, installed NI fan blowing straight up.

01:09:29.359 -> Temperatures:
01:09:29.359 -> BAY1: 18
01:09:29.359 -> BAY2: 26 (outside: -14)
01:09:29.393 -> BAY3: 23 

04:02:20.145 -> Temperatures:
04:02:20.145 -> BAY1: 21
04:02:20.145 -> BAY2: 22
04:02:20.145 -> BAY3: 19

04:33:16.959 -> Temperatures:
04:33:16.959 -> BAY1: 21
04:33:16.959 -> BAY2: 22
04:33:16.959 -> BAY3: 18

...

Test5:
-12S power stays the same
-Middle 18S power decreases slightly
-Outer 18S power increases slightly

12S: 176V@126mA = 22.2 W
18S: 115V@122mA = 14.0 W
18S: 125V@132mA = 16.6 W (using larger lambda gen with lower resolution)

Changed voltages at 4:38AM 2022DEC24

04:39:31.711 -> Temperatures:
04:39:31.711 -> BAY1: 21
04:39:31.711 -> BAY2: 22
04:39:31.711 -> BAY3: 18

04:41:57.512 -> Temperatures:
04:41:57.548 -> BAY1: 21
04:41:57.548 -> BAY2: 21
04:41:57.548 -> BAY3: 19

11:21:16.166 -> Temperatures:
11:21:16.166 -> BAY1: 23
11:21:16.166 -> BAY2: 19
11:21:16.199 -> BAY3: 19

...

Test6:
12S power reduced slightly:

12S: 170V@121mA = 20.6 W
18S: 115V@122mA = 14.0 W
18S: 125V@132mA = 16.6 W (using larger lambda gen with lower resolution)

11:23:49.200 -> Temperatures:
11:23:49.200 -> BAY1: 24
11:23:49.200 -> BAY2: 20 (outside:-8)
11:23:49.200 -> BAY3: 19

15:24:04.461 -> Temperatures:
15:24:04.461 -> BAY1: 26
15:24:04.461 -> BAY2: 23 (outside:-3)
15:24:04.461 -> BAY3: 23

...

Test7:
12S power reduced slightly:
12S: 166V@118mA = 19.6 W
18S: 115V@122mA = 14.0 W
18S: 125V@132mA = 16.6 W (using larger lambda gen with lower resolution)

15:27:48.814 -> BAY1: 26
15:27:48.814 -> BAY2: 23
15:27:48.814 -> BAY3: 23

15:49:47.501 -> BAY1: 26
15:49:47.501 -> BAY2: 23
15:49:47.501 -> BAY3: 24

16:14:57.432 -> BAY1: 26
16:14:57.432 -> BAY2: 24
16:14:57.432 -> BAY3: 24

...

Test8:
12S power reduced slightly:
12S: 163V@116mA = 18.9 W
18S: 115V@122mA = 14.0 W
18S: 125V@132mA = 16.6 W (using larger lambda gen with lower resolution)

16:16:59.295 -> BAY1: 26
16:16:59.295 -> BAY2: 24
16:16:59.295 -> BAY3: 24

16:42:33.764 -> BAY1: 26
16:42:33.764 -> BAY2: 24
16:42:33.764 -> BAY3: 24

18:15:28.160 -> BAY1: 27
18:15:28.160 -> BAY2: 26
18:15:28.160 -> BAY3: 26

20:51:38.459 -> BAY1: 26
20:51:38.459 -> BAY2: 26
20:51:38.459 -> BAY3: 25

05:22:03.682 -> BAY1: 25
05:22:03.717 -> BAY2: 25
05:22:03.717 -> BAY3: 25

Above was 18S--

...

Test9:
Same power as above, but now in 18S+- configuration (to see if middle module gets too hot again).

05:49:18.844 -> LiBCM v0.8.4j, 2022NOV28

05:53:05.587 -> BAY1: 21
05:53:05.587 -> BAY2: 23
05:53:05.587 -> BAY3: 23

12:15:11.992 -> BAY1: 27
12:15:11.992 -> BAY2: 35 (outside: -2)
12:15:11.992 -> BAY3: 28

12:54:33.085 -> BAY1: 28
12:54:33.085 -> BAY2: 35
12:54:33.085 -> BAY3: 29

...

Test10:
2022DEC25

Back to 18S-- configuration (we'll deal with 18S+- later).
Quite a few changes:
-Each 18S heater PCB has:
	QTY2 fewer resistors on the 1st closest cell to LiBCM
	QTY2 fewer resistors on the 2nd closest cell to LiBCM
	QTY1 fewer resistor  on the 3rd closest cell to LiBCM
-Each 12S heater PCB is unmodified from previous tests.
-There's a 10 watt resistor bolted to the aluminum plate on each module.

Cells were inside for four hours, giving them time to heat back up.
Verified cells were all the same temperature with thermal imager.

12S: 163V@116mA = 18.9W
18S: 115V@127mA = 14.6W
18S: 125V@138mA = 17.3W
Plate Resistors: 30V@1A = 30.0W
-------------------------------
Total power: 80.8W

16:23:41.756 -> LiBCM v0.8.4j, 2022NOV28

16:23:47.530 -> Temperatures:
16:23:47.530 -> BAY1: 17
16:23:47.530 -> BAY2: 18
16:23:47.530 -> BAY3: 17

17:18:51.863 -> BAY1: 24
17:18:51.863 -> BAY2: 23
17:18:51.863 -> BAY3: 22

18:14:35.803 -> BAY1: 27
18:14:35.803 -> BAY2: 26
18:14:35.803 -> BAY3: 24

21:22:42.738 -> BAY1: 31
21:22:42.738 -> BAY2: 31
21:22:42.738 -> BAY3: 27

21:43:56.721 -> BAY1: 31
21:43:56.721 -> BAY2: 31
21:43:56.721 -> BAY3: 27

00:14:18.760 -> BAY1: 32
00:14:18.760 -> BAY2: 32 (outside: -7)
00:14:18.760 -> BAY3: 28

...

Test11:
2022DEC26

Same as above, except this time I've stuffed both sides with foam (btwn junction board and 12S, and on opposite side btwn 18S and plastic cover)

12S: 163V@116mA = 18.9W
18S: 115V@127mA = 14.6W
18S: 125V@138mA = 17.3W
Plate Resistors: 30V@1A = 30.0W
-------------------------------
Total power: 80.8W

00:50:15.067 -> LiBCM v0.8.4j, 2022NOV28

(cells previously warm)
00:54:23.460 -> BAY1: 27
00:54:23.460 -> BAY2: 27
00:54:23.460 -> BAY3: 26

01:31:42.474 -> BAY1: 34
01:31:42.474 -> BAY2: 30
01:31:42.474 -> BAY3: 31

01:47:02.189 -> BAY1: 35
01:47:02.189 -> BAY2: 30
01:47:02.189 -> BAY3: 32

Wow, adding that foam really helps!

...

Test 12:
Reduced 12S and outer 18S power:
12S: 148V@105mA = 15.5W
18S: 115V@127mA = 14.6W
18S: 115V@127mA = 14.6W
Plate Resistors: 28V@930mA = 26.0W
-------------------------------
Total power: 71.2W

Test12 begins immediately after Test11.

02:00:18.676 -> BAY1: 36
02:00:18.676 -> BAY2: 30
02:00:18.676 -> BAY3: 33

02:07:44.149 -> BAY1: 35
02:07:44.149 -> BAY2: 30
02:07:44.149 -> BAY3: 33

03:25:06.935 -> BAY1: 36
03:25:06.935 -> BAY2: 31 (outside: -7)
03:25:06.935 -> BAY3: 35

05:34:40.762 -> BAY1: 36
05:34:40.762 -> BAY2: 32 (outside: -7)
05:34:40.762 -> BAY3: 37

...

Test13:
Decrease all power, except bay2 (odd)
12S: 136V@096mA = 13.0W (-2.5W)
18S: 115V@127mA = 14.6W
18S: 104V@115mA = 12.0W (-2.6W)
Plate Resistors: 27V@900mA = 24.3W (-1.7W)
-------------------------------
Total power: 63.9W

Turned fan off, which was previously sitting on top of battery, in middle, directly above middle module, blowing upwards.  This might have been cooling down middle module more than others.

05:44:30.933 -> BAY1: 36
05:44:30.933 -> BAY2: 32
05:44:30.933 -> BAY3: 37

05:48:57.816 -> BAY1: 36
05:48:57.816 -> BAY2: 31
05:48:57.816 -> BAY3: 37

13:42:20.667 -> BAY1: 36
13:42:20.667 -> BAY2: 36 (outside: -1)
13:42:20.702 -> BAY3: 37

Note: Looks like I didn't wait long enough for temp to settle (see higher temperatures during next test)

...

Test14:
2022DEC27
Same as Test13, except we're now using 18S+- configuration (real 18S+)
12S: 136V@096mA = 13.0W
18S: 115V@127mA = 14.6W
18S: 104V@115mA = 12.0W
Plate Resistors: 27V@900mA = 24.3W
-------------------------------
Total power: 63.9W

Modules starting at low temperature.

19:19:33.439 -> LiBCM v0.8.4j, 2022NOV28

19:20:22.785 -> BAY1: 16
19:20:22.785 -> BAY2: 17
19:20:22.785 -> BAY3: 16

20:20:19.713 -> BAY1: 25
20:20:19.747 -> BAY2: 26
20:20:19.747 -> BAY3: 23

20:26:41.932 -> BAY1: 25
20:26:41.932 -> BAY2: 26
20:26:41.932 -> BAY3: 24

20:46:06.765 -> BAY1: 27
20:46:06.765 -> BAY2: 28
20:46:06.765 -> BAY3: 25

21:46:34.927 -> BAY1: 30
21:46:34.927 -> BAY2: 32
21:46:34.927 -> BAY3: 28

22:26:22.753 -> BAY1: 32
22:26:22.753 -> BAY2: 34
22:26:22.753 -> BAY3: 30

01:00:00.590 -> BAY1: 36
01:00:00.590 -> BAY2: 39
01:00:00.590 -> BAY3: 34

01:56:08.657 -> BAY1: 37
01:56:08.657 -> BAY2: 40
01:56:08.694 -> BAY3: 35

03:15:32.694 -> BAY1: 38
03:15:32.694 -> BAY2: 41
03:15:32.694 -> BAY3: 37

07:07:03.360 -> BAY1: 39
07:07:03.360 -> BAY2: 43 (outside: -2)
07:07:03.360 -> BAY3: 39

//

Overall results:

12S:
-PCB sinks around 13 watts.
-Total PCB ESR is 1417 Ohms with 2k0 resistors populated.
Therefore, if we want 13.0 watts with 187 volts (3.9*48), then each discrete resistor on the 12S PCB should be 3781 ohms. Derivation for 13 watts total sunk into 12S:
(136 volts)^2 / (QTY9 * 2000 ohms = (187 volts)^2 / (QTY9 * 3781 ohms) 
We'll use a 3900 ohm resistor (+3.1%), because I already have a reel.

18S: 
-Both 18S PBCs are identical.
-Each PCB sinks around 13 watts.
-QTY2 75 Ohm resistors on two strings closest to LiBCM
-QTY1 75 Ohm resistor on next-closest string
-Total PCB ESR is 905 Ohms with 2k0 resistors populated (including 75 Ohms above).
Therefore, if we want 13 watts with 187 volts (3.9*48), then each discrete resistor on the 18S PCB should be 5941 ohms.  Derivation for 13 watts total sunk into 18S:
x^2/905 = 13, so x is 108.5 volts.
(108.5 volts)^2 / (QTY9 * 2000 ohms) = (187 volts)^2 / (QTY9 * 5941 ohms)
-To match the 12S resistance, we want a 6124 ohm resistor (5941 + 3.1%) 
We'll use a 6200 ohm resistor (+4.4%), because that's what's in stock.  FML.

Bolt on resistors:
-Identical construction for both 18S+- & 18S--
-In total sinks 24 watts (8W/resistor).
-At 187 volts (3.9*48), total string resistance is ideally 1457 ohms.
-Each discrete resistor is ideally 485 Ohms. 
-We'll use QTY3 500 Ohm bolt on resistors in series, which yields 1500 Ohm ESR.
-Discrete resistors sink 23.4 watts @ 3.9 V/cell (combined).
-Discrete resistors sink 17.8 watts @ 3.4 V/cell )combined).

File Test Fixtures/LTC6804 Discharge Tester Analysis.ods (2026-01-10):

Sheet: Sheet1
Paste RAW output from Arduino Serial Monitor Window here (delimiters: ',' & '>')
 | 23:22:58.194 - | bitmapPattern: 0
 | 23:22:58.730 - | IC0 | 3.341 | 3.33 | 3.327 | 3.327 | 3.332 | 3.331 | 3.334 | 3.327 | 3.332 | 3.333 | 3.333 | 3.332
 | 23:22:58.730 - | IC1 | 3.339 | 3.329 | 3.331 | 3.335 | 3.332 | 3.33 | 3.342 | 3.331 | 3.333 | 3.332 | 3.335 | 3.344
 | 23:22:58.730 - | IC2 | 3.334 | 3.333 | 3.331 | 3.332 | 3.331 | 3.327 | 3.333 | 3.33 | 3.33 | 3.331 | 3.332 | 3.338
 | 23:22:58.768 - | IC3 | 3.335 | 3.33 | 3.328 | 3.331 | 3.329 | 3.33 | 3.335 | 3.331 | 3.333 | 3.333 | 3.33 | 3.332
 | 23:22:58.768 - | IC4 | 3.331 | 3.331 | 3.337 | 3.335 | 3.332 | 3.331 | 3.33 | 3.333 | 3.33 | 3.329 | 3.328 | 3.333
 | 23:22:58.768 -
 | 23:22:58.768 - | bitmapPattern: 10101010101
 | 23:22:59.296 - | IC0 | 2.246 | 4.428 | 2.24 | 4.425 | 2.24 | 4.43 | 2.242 | 4.424 | 2.241 | 4.433 | 2.241 | 4.422
 | 23:22:59.296 - | IC1 | 2.248 | 4.415 | 2.243 | 4.421 | 2.245 | 4.413 | 2.248 | 4.428 | 2.241 | 4.431 | 2.24 | 4.436
 | 23:22:59.335 - | IC2 | 2.25 | 4.417 | 2.248 | 4.419 | 2.244 | 4.415 | 2.246 | 4.422 | 2.242 | 4.426 | 2.242 | 4.424
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

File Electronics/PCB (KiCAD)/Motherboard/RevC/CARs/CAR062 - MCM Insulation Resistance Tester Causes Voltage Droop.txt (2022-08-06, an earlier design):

Existing hardware only has HVDC<->GND capacitors from HVDC- to GND_ENG.
It's possible we need a complimentary pair going from HVDC+ to GND_ENG.

Another thought is that both these capacitor pairs should go to GND_CHASSIS (instead of GND_ENG).  However, that would be difficult since GND_ENG is used inside LiBCM.

/////////////////////////////////////////////////////////////////////////////////

Solution:

Added coupling capacitors from HVDC_POS_FUSED to 12NEG_RAW.

Done

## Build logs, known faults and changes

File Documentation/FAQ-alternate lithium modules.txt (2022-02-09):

FAQ - Lithium Battery - Other Configurations

Q: Will LiBCM work with other (non-EHW5) lithium modules?
A: Yes, but it will require custom mechanical fitment (e.g. HVDC current and BMS ribbon cables).
A: Linsight will create custom-length ribbon cables to any length.
A: You must determine how to correctly connect these cables to each cell/module.
A: At present, LiBCM only supports 48S configurations.
A: Without firmware modifications, LiBCM supports batteries from 0.5 Ah to 65.5 Ah.
A: Linsight only officially supports EHW5 lithium modules.

Q: Which lithium chemistries does LiBCM work with?
A: LiBCM's hardware supports all known lithium cell chemistries.  Specifically, LiBCM supports any cell that charges with a CC/CV profile.
A: At present, LTO & LiFePO4 modules are NOT supported in firmware.
A: The firmware defaults attempt to keep each cell between 3.47 volts (10% SoC) and 4.01 volts (85% SoC), with absolute max values between 3.01 volts (0% SoC) and 4.2 volts (100% SoC).  
A: These values can be changed (at your own risk) to any value between 1.1 & 5.0 volts.

Q: How many cells in series does LiBCM support?
A: The hardware supports from 4S to 60S.
A: At present, the firmware only supports 48S.

Q: Can LiBCM work with packs larger than 60S?
A: Not easily.  You would need to connect an additional BMS PCB to LiBCM's SPI bus, and then rewrite the firmware to talk to it.  It's possible, but you're on your own.

Q: Can LiBCM work with packs less than 36S?
A: Probably not, as the pack voltage becomes too low for the OEM MCM, which severely limits assist below 120 volts.
A: If the voltage drops too low, the MCM will enable force background charging, which could overcharge packs less than 36S.

Q: Can I use LiBCM with the original NiMH cells?
A: Yes, but you'd need to change the firmware.  I will not help you do that.
A: I can't think of a reason why you'd want to do this.

Q: Can I use LiBCM without any battery at all (e.g. as a defeat device to pass emissions)?
A: Per 42 USC 7522: defeating an emissions component is felony in the United States.  LiBCM's firmware will not work unless a lithium battery is connected.

Q: Why would placing the fuse/switch between modules 2 & 3 damage LiBCM?
A: Six cells in each of these two modules share a single voltage monitoring IC, which is only rated to measure up to 8 volts per cell.  If the fuse and/or switch are installed between modules 2 & 3 - and the fuse blows and/or the switch is turned off - then the entire pack voltage would develop across one measurement circuit.  This would (safely) destroy the LiBCM PCB.
A: The ideal solution is to use a different IC (e.g. LTC6813, which is unavailable due to the Great Chip Shortage).

Q: Considering the abundance of 18S modules, and that a 54S (18S*3) setup fits inside the OEM enclosure, why does LiBCM presently only support 48S?
A: While QTY3 18S modules mechanically fit inside the OEM enclosure, placing an 18S module in bay 1 (closest to the junction board) prevents the high current cables from cleanly routing to the junction board.  
A: Numerous firmware changes are required to support 54S.
A: The OEM DCDC converted will not work above ~218 volts.
A: Due to other hardware issues**, the increased voltage from a 54S pack only increases assist power by ~8% (compared to an equivalent 48S pack).
**Primary limitation: LiBCM can only spoof the actual pack voltage down to 67%. Since the MCM reduces current as the (spoofed) pack voltage increases, the higher voltage developed by a 54S pack will cause the MCM to reduce output current, hence the output power is also reduced.  Adding additional external resistors might resolve this problem (TBD). 

Q: When will the LiBCM firmware support 54S?
A: No idea, but not anytime soon.  If you want to use LiBCM anytime soon, you should use a 48S battery.
A: When 54S ships, it will require a few cable changes and a new BMS adapter.  The LiBCM PCB itself won't require any changes.  

Q: When will the LiBCM firmware support 60S?
A: No idea, but probably never with standard lithium cells (4.2 Vmax).  The resulting voltage is too high for the OEM IMA system (but not for LiBCM), and requires substantial hardware modifications.  Certainly a different HVDCDC converter is required. 
A: 60S is primarily intended for LiFePO4 cells (3.7 Vmax).  

Q: How do I use LiBCM with a larger pack?
A: EHW5 modules are easily reconfigurable; the cells are bolted together, rather than tab welded.  It takes around an hour to reconfigure an 18S1P pack to either 9S2P, 6S3P, or 3S6P.  Reconfiguring QTY8 18S modules to 6S3P yields a 15Ah 48S module.
A: A cheaper option is to purchase a larger battery.
A: In either case, you'd also need to connect custom BMS ribbon cables to each module; contact Linsight for more details.

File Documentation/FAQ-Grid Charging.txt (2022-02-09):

Q: What input voltages does the grid charger support?
A: 100 Vac to 250 Vac
A: 50 or 60 Hz

Q: How do I grid charge LiBCM?  
A: With the key off, plug LiBCM's NEMA 5-15P power cable into an extension cord.
A: The LCD display will display the state-of-charge, max/min/delta cell voltages, and temperature.
A: LiBCM automatically charges and balances the cells as needed.
A: LiBCM's onboard fans automatically activate as needed to heat or cool the IMA battery.
A: You can unplug the grid charger whenever you want.
A: If the battery SoC is too low, LiBCM will turn off ten minutes after the key turns off.  In this case, you must plug the grid charger in before LiBCM turns off (or else the grid charger won't charge).

Q: Can I leave the grid charger plugged in indefinitely?
A: Yes.  LiBCM 100% handles grid charging, just like any other modern lithium device.

Q: Why should I grid charge?
A: Starting with a full IMA battery improves fuel economy.
A: With the OEM NiMH cells, grid charging is primarily used to balance the cells.  Since LiBCM balances cells whenever the car is off, grid charging is never required to balance cells.

Q: Is grid charging required?
A: If the car is used regularly, grid charging is never required.
A: For long term storage, grid charging is required if the IMA switch is left on.

Q: How long can I leave my LiBCM-equipped Insight parked without driving or charging (e.g. at the airport)?
A: If SoC drops below 9%, LiBCM will turn itself off, which reduces consumption to 0.1% SoC per month.  Therefore, you can park your car for several years without damaging the battery.  However, discharging the pack below 10% decreases overall battery lifetime, so ideally the pack shouldn't drop below 10% SoC.
A: During the Open Beta, LiBCM power-on consumption is ~25% SoC per month.  Therefore, you should drive or grid charge the vehicle at least monthly (to keep the SoC above 10%). 
A: A future firmware update should reduce power-on consumption to ~2% SoC per month.  Therefore, you should drive or grid charge the vehicle at least yearly (to keep the SoC above 10%).

Q: I plan to park my vehicle for longer than the above-indicated time.  How can I prevent over-discharge?
A: Turn the IMA switch off, which drops power consumption zero.  You can store the car indefinitely.  Ideal storage SoC is 50%.
A: Leave the IMA switch on, and plug in the grid charger.  You can store the car indefinitely.
A: Charge the pack prior to long-term parking (each 2% SoC increase adds another month to long term storage).

Q: How long does it take to balance a lithium pack?
A: When LiBCM is first installed in the car, if the SoC is drastically different between any two cells/modules, then it could take several days to balance the cells.  It's ok to drive the car with an unbalanced pack, but that will limit SoC range. 
A: Healthy lithium packs spend at most a few hours balancing each month.
A: Unhealthy packs should still rebalance completely overnight.
A: Balancing occurs automatically whenever the car is off, as long as the pack is sufficiently charged.
A: Plugging the grid charger in allows the modules to balance faster, as the fans can run continuously.

Q: Why does it take so long to balance the lithium cells?
A: LiBCM balances cells by connecting a 75 Ohm resistor in parallel to each 'full' cell.  LiBCM balances cells near 3.9 volts, hence LiBCM can only discharge full cells at 52 mA (200 mW/cell).  Since each 5 Ah EHW5 cell contains 18.5 Wh of energy, if you were to install one completely empty module (0% SoC) and another completely full module (100% SoC), then the worst-case balancing time would be 92 hours.

Q: Why is the grid charger so slow?
A: Cost.
A: LiBCM supports the following grid chargers (charge times are for a 48S EHW5 pack from 10% to 75% SoC):
-charge pack in 7.5 hours: PLED96W-213-C0450-D (included in LiBCM purchase price)
-charge pack in 2.3 hours: HLG-320H-C1400B
-charge pack in 1.5 hours: HLG-480H-C2100B (requires higher-current 5x20mm fuses)
-charge pack in 0.7 hours: HVGC-1000A-M-AB (requires higher-current 5x20mm fuses and 240 volt mains)
-charge pack in 0.3 hours: GEN200-16.5 (contact Linsight for full modification list).
A: Other grid chargers might work if they meet the following criteria:
	-constant current supply
	-must output voltage between at least 139:207 volts (with 48S lithium cells)
	-output current must be controllable via a PWM pulse train.

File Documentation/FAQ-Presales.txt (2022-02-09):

Q: How do I pronounce the name?
A: Layman's terms: Say the five letters separately (L, I, B, C, M)
A: Phonetic: El+Eye+Bee+Sea+'Em 
A: IPA: 'ɛl'aɪˈbiˈsiˈɛm`

Q: What is "LiBCM"
A: "Lithium Battery Condition Monitor"
A: A drop-in replacement computer that allows safe lithium battery operation in the G1 Honda Insight (2000-2006).

Q: What is "Linsight"?
A: Previously: an unreleased hardware project (circa 2016), which morphed into "LiBCM".
A: Now: "Lithium Insight", the company that designed and manufactured "LiBCM".

Q: What new features does LiBCM add?
A: More power!  LiBCM can more than double the electric motor's power output.
A: Effortless grid charging comes standard.  Plug LiBCM into an extension cord; LiBCM handles the rest.
A: Built-in cell balancing whenever the car is off.
A: Per-cell voltage measurements.  Diagnose pack issues down to each cell.
A: Custom LCD screen reports real-time hybrid pack data to the driver.
A: Advanced USB diagnostic data.  Log data to your computer as you drive.
A: USB firmware updates... add new features as they become available

Q: Will LiBCM make my car faster?
A: Absolutely.  The difference is night-and-day.
A: Adding the +40% current hack PCB (sold by ic.net user "@Bull Dog") will add even more power.
A: Once you drive an LiBCM-equipped Insight, you'll never want to switch back.
A: Testimonial: youtube.com/watch?v=srkx_Rq2-ro

Q: With all this additional power, can Insight spin the tires off the line?
A: Only when the road is wet or has debris... it's still a Honda Insight... just more powerful.

Q: Does LiBCM work in any other vehicles besides the G1 Honda Insight (2000-2006)?
A: No.  LiBCM is only designed for the G1 Honda Insight.
A: LiBCM is a passion project.
A: With minimal effort (mostly mechanical fitment), LiBCM will probably work in the G1 Honda Civic Hybrid.
A: With dedicated engineering effort, LiBCM could probably work with most NiMH-based hybrid vehicles.
A: I'm not interested in adapting LiBCM to your vehicle (except as a paid consultant).

Q: Do I really need a battery management system (BMS) to use lithium batteries?
A: Most lithium battery chemistries are unstable beyond a narrow voltage range.  Charging/discharging cells beyond this range can cause a thermal event (i.e. fire).
A: Operating a lithium battery without a BMS might work initially, but isn't safe.

Q: What's included with the "DIY LiBCM Kit"?
A: Everything except the actual lithium battery modules.
A: Complete details: linsight.org/kit

Q: Where do I purchase lithium battery modules?
A: See linsight.org/kit

Q: Does LiBCM work with CVT transmissions?
A: Yes.

Q: Does LiBCM work with 2005 & 2006 Honda Insights?
A: Yes.

Q: How long does it take to install a DIY LiBCM Kit?
A: At this point I can do a full swap in a couple hours, so expect to spend between two and eight hours start to finish. It's a lot of work.

Q: Is LiDisplay included with the DIY LiBCM Kit?
A: No.  It hasn't been designed yet.  For now, a basic 4x20 debug LCD is included.
A: Once LiDisplay exists, it will be sold as a separate product.

Q: Is LiBCM better than the OEM computer it replaces?
A: Absolutely, and in every possible way.  The OEM BCM is garbage.

Q: What is a "Drop-In LiBCM Battery"?
A: A completely assembled lithium battery - contained within the original plastic battery housing - with the LiBCM computer already connected and ready to go.  Installation is nearly identical to an OEM battery (see www.linsight.org/install/libcm-equipped-battery).  

Q: Where do I purchase a Drop-In LiBCM Battery?
A: BumbleBatteries.com is the primary Drop-In LiBCM Battery distributor.
A: The following insightcentral.net members are authorized to install 
A: I do not sell Drop-In LiBCM Batteries directly to customers.  However, I do offer an "LiBCM Kit" for sale to anyone who can pass my safety quiz.

Q: How difficult is it to convert an OEM battery using the DIY LiBCM Kit?
A: DIY installation instructions are available here: linsight.org/install/diy-libcm-kit

Q: What is LiBCM's warranty period?
A: "Drop-In LiBCM Batteries" are warranted per the terms of the authorized reseller.
A: From a legal standpoint, "DIY LiBCM Kits" are provided as-is, without any warranty whatsoever.  Note that each DIY LiBCM Kit is 100% test driven prior to shipment.
A: I will make reasonable efforts to repair defective components at my actual cost, regardless of fault.  If the LiBCM PCB cannot be safely repaired, I will replace the entire PCB at a reduced cost. 
A: On a case-by-case basis, if I determine the failure occurred at no fault of the user, I will repair the PCB for free, excluding shipping costs.

Q: Where is LiBCM manufactured?
A: In my garage in Chattanooga, TN, using globally sourced parts.
A: Here's a video: https://www.youtube.com/watch?v=lkyL85lTiGc

Q: What portions of the original hybrid system does LiBCM replace?
A: The original "Battery Condition Module" computer ('BCM') and the NiMH cells.
A: Complete list of removed OEM parts: www.youtube.com/watch?v=5RkxeL5m9-A

Q: What parts of the original IMA system are modified by LiBCM?
A: The IMA wire harness has a single wire cut and spliced.  Easily revertible.
A: The battery temperature harness has two wires cut and shortened.  Easily revertible.
A: The battery voltage tap harness (with orange side plate) has two wires cut.  Easily revertible as long as you only cut those two wires (more details in installation videos).
A: Full details: linsight.org/install/diy-libcm-kit/modify-oem-parts

Q: Is the LiBCM Kit dangerous to install?
A: Absolutely.  LiBCM can easily kill you if you don't follow the installation instructions.  Safety videos are provided as needed during the conversion process.

Q: What happens if my Insight is in a wreck?
A: Hopefully you're ok.
A: If you follow the installation instructions, LiBCM isn't any less safe than OEM.
A: LiBCM includes 1/8" aluminum mounting brackets to secure the lithium modules inside the OEM battery enclosure.

Q: How is LiBCM shipped?
A: USA: Flat rate shipping (UPS or USPS) is included in the purchase price.
A: Other: The first $20 is included in the purchase price.  You pay the difference based on the actual USPS rate.

Q: What is LiBCM's recommended ambient operating temperature range?
A: -30 degC to 55 degC

Q: What aftermarket accessories are compatible with LiBCM?
A: Any accessory whose wiring doesn't physically connect to wires inside the IMA bay.
A: Any accessory that modifies the signals between the MCM & ECM (e.g. IMAC&C).
A: Most current hack implementations.  However, LiBCM can spoof the battery current sensor value in software.  Linsight recommends installing @Bull Dog's MCM Current Hack PCB (sold separately).

Q: What aftermarket accessories are NOT compatible with LiBCM?
A: Any and all NiMH-based grid chargers, which are dangerous to use with LiBCM.  LiBCM's built-in grid charger makes these unnecessary.
A: Dischargers of any kind.  LiBCM's built-in balancing hardware makes these unnecessary. 
A: Any device that intercepts/modifies data from the BATTSCI data bus (which routes from the BCM to the MCM).

Q: Do I need to install a larger fuse to use LiBCM?
A: Only if you also add the MCM Current Hack PCB.

Q: My IMA/CEL light is on with my existing NiMH battery.  Will LiBCM 'fix' that?
A: LiBCM will not work unless the IMA system is entirely present and functional, except that the OEM BCM and the NiMH cells can be in any condition (because LiBCM replaces them entirely).  Everything else in the IMA system must work prior to installing LiBCM.

Q: Will the car still run if LiBCM fails?
A: Yes.  If the IMA system fails, the car will use the backup starter (just like OEM).
A: LiBCM won't leave you any more stranded than an OEM pack will.
A: In an error condition where LiBCM is at-fault, unplugging the BCM connector will allow the IMA system to charge the 12 volt battery (with a CEL).
A: Unless the PCB is damaged, LiBCM will continue monitoring cell voltages even when the BCM connector is unplugged. If a cell gets too high/low, a buzzer will sound (whether or not the vehicle is on).  If you continue driving the vehicle while the buzzer is on, the lithium modules could catch on fire.   

Q: Will LiBCM improve my mileage?
A: If your old pack is toast, then yes.
A: Otherwise, it entirely depends on driving habits.
A: My mpg hasn't changed, but I drive the car much faster/harder now.
A: (Beta) the default voltage spoofing algorithm isn't yet optimized for fuel efficiency.
A: LiBCM supports several different charge profiles.  For example, if you always drive short distances and grid charge when parked, you can tell LiBCM to limit/disable regen.  See config.h for more info.

Q: Why is LiBCM so expensive?
A: It's not.

Q: If I decide the DIY LiBCM Kit isn't for me, can I get a refund?
A: Yes, and you don't need to state a reason.  I will refund your entire purchase price - minus my actual costs** - for any reason whatsoever.  
A: I do not sell Drop-In LiBCM Batteries directly to end users (only DIY LiBCM Kits).  Therefore, if you purchase a Drop-In LiBCM Battery from an authorized installer and decide it isn't for you, then you'll need to contact the installer directly (and go by their terms).
**I will not refund the following fees:
-Actual shipping costs, and/or;
-Fees that PayPal doesn't refund.  If you paid using "friends & family", then that fee is $0.30.  If you paid using "commercial service", then that fee is $35.17, and/or;
-LiBCM Kit parts that are returned damaged; I will charge a reasonable fee to cover the repair.

Q: If I decide to remove LiBCM, how difficult is it to 'go back' to the stock NiMH configuration?
A: Since LiBCM only modifies components within the original battery enclosure, the simplest method is to swap your LiBCM-equipped IMA battery enclosure with an unmodified NiMH pack.  In that case, the only residual modification is the single cut wire on the IMA wire harness.  Reconnecting that wire is trivially easy: just plug the ORG & WHT Anderson connectors into each other.  That's it... now your car is NiMH again.
A: If there's any chance you might want to revert back to NiMH later (using the same battery enclosure), follow the specific "I might go back" instructions noted in these videos: linsight.org/install/diy-libcm-kit/modify-oem-parts
There will be a few leftover holes, but they do not affect the original NiMH functionality.

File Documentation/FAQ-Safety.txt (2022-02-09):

FAQ - Safety

Q: What safety features does LiBCM use to prevent electrocution?
A: All low voltage signals interfacing with LiBCM are galvanically isolated from all high voltage signals.  You can actually hold the PCB up to a bright light and see the clearance.  The entire LiBCM PCB can burn to a crisp and there's zero chance the HVDC will bridge to the low voltage control signals.
A: Both HVDC+ and HVDC- are isolated from chassis ground.  In theory, touching either HVDC signal will not result in shock, even if you are also touching chassis ground.  You would need to touch BOTH HVDC signals at the same time to receive an electric shock.
A: The MCM constantly monitors for HVDC faults to chassis ground. If a ground fault is detected, the MCM will open the HVDC contactor and set the check engine light.
A: LiBCM is completely surrounded by a touch-proof polycarbonate cover.  LiBCM will set a check engine light if that cover isn't installed.

Q: Is it safe to touch the exposed metal prongs on the grid charger power cable?
A: Yes.  There are redundant diodic and galvanic isolation barriers between the IMA HVDC bus and the 5-15P plug.  The galvanic isolation barrier is continuously tested by the MCM whenever the key is on.

Q: Does LiBCM safely manage cell voltage under all conditions?
A: Probably.  That's certainly the goal.
A: If the voltage goes out-of-bounds, LiBCM will emit an audible beep and disable the IMA system, which will prevent further charge/discharge... unless you've hacked the IMA system that prevents this... in that case, you're on your own.  If LiBCM is installed in an otherwise OEM vehicle, then over/under-charging is unlikely.

Q: Is it safe that LiBCM's high current cables use 75 amp rated Anderson connectors, even though the IMA system can pull 140 amps?
A: Yes.
A: The nominal 75 amp rating is for a continuous load, and with the additional heat-load introduced by adjacent multi-gang connectors (which are not present in LiBCM).
A: Anderson rates this connector to 120 amps for five minutes (per UL 1977 testing).  The IMA system cannot maintain currents this high for this long (so this connector is not the weakest link).
A: This specific connector has been used in various IMA-related projects for 15+ years. 

Q: Why does the LiBCM cover say "Hazardous voltage present under this cover, even when IMA switch is off"?
A: UL requires a warning whenever exposed voltages greater than 60 VDC are present and likely to come into contact with a service technician. 
A: Turning the IMA switch off splits the pack into two separate modules.  However, since the combined pack voltage exceeds 120 volts, it follows that at least one (or both) separated modules will exceed 60 VDC.
A: When LiBCM's cover is installed, LiBCM does not expose any HVDC signals to the user.

Q: What certifications does LiBCM have?
A: None, only my many years of experience as an EE.  It's a passion project.
A: LiBCM is exempt from FCC emissions testing requirements, per 15.103(A), which exempts "digital devices utilized exclusively in any transportation vehicle".
A: LiBCM does not violate 42 USC 7521 ("emissions defeat device"), per subsection (c)(3).
A: LiBCM is legal to operate on roadways in the United States, per 40 CFR parts 85 & 86.
A: UL/CE/etc testing is not required to sell LiBCM in the USA or UK.  However, LiBCM is not legal for sale in the EU (which requires CE approval).

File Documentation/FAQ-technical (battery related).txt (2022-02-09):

FAQ - Lithium Battery - 48S EHW5 Configuration

Q: Why is the 18S+/18S+/12S+ module configuration not supported?
A: The high current leads are too long, difficult to route, and require two separate manual disconnects.  This increases RF noise inside the IMA bay, which increases the serial data error rate.
A: There are far fewer 18S+ modules than there are 18S- modules. 

Q: How 'hard' is LiBCM pushing the EHW5 modules?
A: Way below spec.
A: LiBCM would theoretically approach the EHW5's limits around 53 kW assist.  LiBCM presently delivers less than half that value.

Q: How much lighter is an LiBCM-equipped battery pack?
A: A complete OEM NiMH pack weighs 73 pounds (including MCM & BCM).
A: A complete LiBCM-eqipped EHW5 pack weighs 62 pounds (with MCM & grid charger).

Q: Can I convert an 18S+ lithium EHW5 module to 18S- (or 18S- to 18S+)?
A: No, or rather it's not officially supported.
A: Linsight created a working prototype (by flipping the individual cells around), but the concept never made it to production.  
A: You're on your own mechanically if you decide to convert an 18S+/18S- module to 18S-/18S+. The BMS pinout will change, as will the HVDC current cable lengths (the cable posts will be in a different locations).
A: Linsight only supports the configurations shown here: linsight.org/kit.

Q: How long will EHW5 lithium modules last?
A: Panasonic's datasheet specifies 90% capacity retention after 10 years.  EHW5 cells will still work (at reduced capacity) after ten years.
A: At room temperature, the 5 Ah EHW5 cell is rated for 50,000 cycles (10-85% SoC) with a continuous 40 A charge/discharge test.  That's thirteen cycles per day for ten years straight.
A: The cells should die due to old age, rather than cycle count.

Q: What are the best ways to maximize battery life?
A: In warm weather, park in the shade.
A: When temperatures drop below freezing, park in direct sunlight to increase pack temperature.
A: Extreme temperatures will substantially reduce cell life.
A: Limit assist and regen whenever the resting cell voltage delta exceeds 25 mV.  LiBCM automatically balances cells whenever the car is off.
A: Avoid storing LiBCM with a near-empty or near-full battery.

Q: Why does LiBCM limit assist and regen below freezing?
A: To increase battery life.
A: In cold weather, if the cabin temperature is warmer than the battery, LiBCM will draw air into the IMA bay to heat the battery.

Q: What happens 10+ years down the road when these EHW5 cells die?
A: As the cells ESR increases, the cells will unbalance more rapidly while driving.  Whenever the car is off, LiBCM will automatically balance the cells to within 1 mV.
A: Balancing the cells won't 'fix' aging batteries, but it will maximize performance. 
A: All cells will eventually fail. Fortunately, the EHW5 lithium cell geometry seems destined to become a de-facto standard... and if not, then a decade from now we can always have more made specifically for our purpose.  Or maybe another existing lithium pack design will come along that's equally compatible.

Q: How much heat does an EHW5 lithium pack generate internally (due to ESR)?
A; Around ten times less than the OEM NiMH pack (which can generate several kW in heat inside the NiMH sticks).  
A: Empirical testing shows that new cells won't heat up beyond 20 degF above ambient in even the most demanding use cases.
A: EHW5 lithium cells have an initial cell ESR around 1.1 mOhm.
A: LiBCM can briefly deliver 140 amps in assist, which generates ~22 watts in heat inside each cell (1035 watts for the entire pack).
A: LiBCM can continuously deliver 80 amps until the pack is empty.  At this power level, each cell internally generates 7 watts in heat (338 watts for the entire pack).  Each EHW5 is therefore generating about the same heat as a 100 watt incandescent light bulb.
A: In practice, battery self-heating is inconsequential.  The overwhelming contributor to pack heat is the cabin air temperature.
A: LiBCM directly monitors each EHW5 module's outer enclosure temperature.  LiBCM also monitors the cabin air temperature, the exhaust air temperature, the IMA bay temperature, and several other temperatures to verify the pack operates within acceptable temperatures.  LiBCM will disable assist/regen if needed to prevent overheating.

Q: Does a 48S EHW5 lithium battery store more energy than the stock NiMH pack?
A: An LiBCM-equipped IMA battery with QTY48 EHW5 lithium cells stores 30% more deliverable energy than an OEM NiMH pack*.
*An OEM NiMH pack nominally stores 936 Wh, whereas the EHW5 lithium pack only stores 887 Wh.  However, the lithium pack has a wider safe operating SoC range, and can therefore deliver more energy (666 Wh) than the OEM pack (515 Wh).

Q: What's special about cell 19?
A: LiBCM has QTY5 voltage measurement ICs.  Each IC measures QTY12 cells.  Four of the five ICs measure cells that are contained within the same module (e.g. IC1 measures cells 1:12, which are all in the same 18S module; IC3 measures cells 25:36, which are all in the same 18S module; IC4 measures cells 37:48, which are all in the same 12S module; etc).
A: In contrast, IC2 measures cells in two different 18S modules (cells 13:18 are in one 18S module, whereas cells 19:24 are in a different 18S module).  This causes LiBCM to measure not only the actual C19 voltage, but also the voltage drop in the cable between both 18S modules.
A: LiBCM uses an empirically-derived resistance value to cancel out the cable drop voltage.
A: If you're not using EHW5 modules, you can modify (or disable) this feature (search "LTC68042_ENABLE_C19_VOLTAGE_CORRECTION" in config.h)
A: You can blame this oddity on the 2020/2021/2022 global chip shortage... Ideally LiBCM would use the LTC6813 (which measures QTY18 cells per IC).

Q: Where can I find more info on EHW5 modules?
A: Everything I know about these specific modules is located here: github.com/doppelhub/Honda_Insight_LiBCM/tree/main/Electronics/Lithium%20Batteries
github.com/doppelhub/Honda_Insight_LiBCM/tree/main/Mechanicals/Honda%20G3%20Lithium%20Batteries

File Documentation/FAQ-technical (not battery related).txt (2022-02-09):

FAQ - Technical Questions - Non-Battery

Q: How does LiBCM "more than double the original hybrid power output"?
A: Insight's NiMH cells are the weakest link in the original hybrid electric design.  LiBCM replaces the outdated NiMH chemistry with modern lithium cells, which can handle considerably more power.
A: The OEM motor and IGBT module were designed to handle substantially more power than the OEM NiMH battery could deliver.

Q: How much additional power does LiBCM add to the car?
A: A stock IMA system with NiMH cells delivers at most 12 kW (16 horsepower).
A: An LiBCM-equipped pack in a manual transmission car delivers at most 18 kW (24 horsepower)(50% more power).
A: Adding the current hack PCB (https://www.youtube.com/watch?v=wtwM0kgxeJ4) to a manual transmission car increases LiBCM power to at most 24 kW (32 horsepower)(100% more power).
A: Adding the current hack PCB to a CVT car increases LiBCM power to around 21 kW.
A: The above values are only briefly possible in 2nd or 3rd gear.  To access this power at your command, you need a manual IMA control system (sold separately).
A: LiBCM can theoretically deliver around 32 kW (42 horsepower)(e.g. with lower ESR cells and 60S configuration).

Q: Will all this additional power 'hurt' the stock IMA system?
A: The NiMH pack is by far the weakest part of the OEM IMA system.
A: The next weakest part is the IGBT module.  The MCM monitors both current and temperature on this module (and will disable assist/regen as needed).
A: The IMA motor does not have temperature feedback.  However, the 5 Ah EHW5 lithium modules LiBCM is designed for cannot provide regen/assist long enough to overheat the motor (a larger lithium battery could, though).  Anecdotal evidence suggests that discharging an 8x larger pack does not overheat the IMA motor. 
A: Overall, there's low risk that installing LiBCM will damage the IMA system.
A: LiBCM could cause increased wear on mechanical components, due to the increased torque delivered to the wheels.
A: Use LiBCM at your own risk.

Q: Why does LiBCM spoof a lower pack voltage?  Why not send the actual voltage to the other computers?
A: The lithium charge/discharge voltage curve is substantially different from NiMH cells.
A: Sending the actual pack voltage would cause the IMA system to undercharge the lithium modules.
A: Spoofing a lower voltage causes the IMA system to deliver more power to the hybrid motor.
A: LiBCM has several different voltage spoofing profiles.  See config.h for a complete list.

Q: Which specific voltages does LiBCM 'spoof' to increase power?
A: BATTSCI (digital, sent from BCM to MCM)
A: MCM'E' (high voltage, modified with galvanically isolated PWM train)
A: VPIN (LiBCM man-in-the-middles this analog signal (by cutting the ORG wire on the IMA wire harness))
A: Full explanation: https://www.youtube.com/watch?v=5rsAQy2ybBA

Q: Can LiBCM communicate directly with the H-Line serial bus
A: The LiBCM hardware supports it, but it's not supported in firmware.
A: The OEM BCM isn't connected to the H-line either.  Instead, the MCM transmits BCM data to the H-line (e.g. to display SoC on OBDIIC&C).

Q: Does LiBCM ever turn off?
A: LiBCM typically remains on, unless the battery SoC drops below 9%.  This allows LiBCM to balance cells when the car is off, sense when the grid charger is plugged in, and monitor cell voltage and temperature at all times.
A: LiBCM powers on each time the IMA switch is manually turned on.
A: LiBCM powers on whenever the USB cable is connected to a powered host (regardless of IMA switch status).
A: LiBCM powers on whenever the key is in the 'ON' position (and the IMA switch is on).
A: LiBCM can choose to turn itself off (as required).  To turn LiBCM back on, either turn the key on or cycle the IMA switch.

Q: Why does LiBCM use an Arduino Mega2560?
A: LiBCM's production volume is so low that generic Arduino Megas are actually cheaper than just the cost of the MEGA2560 processor.  The Mega also includes two MCUs, a USB port, an oscillator, a voltage reference.
A: It's in stock. I've had zero issues buying them, which is more than I can say for pretty much any other part right now. 
A: V&V is easier when I can remove the MCU as needed to troubleshoot signals... pulling off the entire MCU allows me to inject signals anywhere I want, without having to worry about how the MCU will behave.
A: Mechanical issues would have required a separate PCB for the USB connector anyway.
A: USB firmware updates are easy thanks to Arduino team's dedicated bootloader legwork. This is good for customers.
A: People unfamiliar with embedded development environments can modify the firmware without having to install a complete embedded toolchain (e.g. IAR/Atmel Studio/etc). Arduino is hands down the easiest embedded toolchain out there.
A: LiBCM is nearly feature complete and yet is only using 10% of CPU time, 7% of storage, and 22% of RAM... with an 8b MCU.
A: LiBCM is mostly written in pure C.  A few HAL-specific tasks use the (slower) Arduino API. The Arduino IDE is mostly used for the built-in GCC compiler, plus point-and-click interface.

Q: Should I install the current hack PCB (sold separately)?
A: Yes, but it's not required.  Your friends will stop telling you your car is slow.
A: There aren't any downsides.  If you decide it's not for you, disabling the hack is as simple as toggling four DIP switches and uploading new firmware to LiBCM.

Q: What additional parts do I need to install the current hack?
A: A 150 amp, 175 amp, or 200 amp L50S Littelfuse.
A: LiBCM is specifically designed for use with the (excellent) "Current Hack PCB", designed by @retepsnikrep & @Bull Dog.  See: youtube.com/watch?v=FATCvhCUAjk
A: Older (less simple) current hack hardware will work, too, but you'll need to remove all BCM-related components (which connect to the battery current sensor).  
A: If you'd rather leave the entire existing current hack in place, you can disable LiBCM's software spoofing (and use your existing hardware instead).

Q: Why is the 4x20 LCD going away after the Open Beta period ends?
A: LiDisplay will entirely replace the existing screen.  LiDisplay is a touch screen user interface with a 480*320 color display.  It'll be a huge upgrade.
A: The 4x20 screen's serial architecture is terrible, antiquated, and has odd timing requirements.  LiBCM spends more CPU time servicing the LCD screen than all other CPU tasks combined.
A: The 4x20 screen has a low-level driver bug that causes the CPU to lock up under certain hardware corner cases.  I could write my own driver, but I've worked around the issue enough for now, and would rather focus that energy on the LiDisplay replacement.
A: LiBCM might be able to drive both displays simultaneously.  If so, I'll deprecate the 4x20 display.  If not, I'll write some code to auto-detect which display is connected; if LiBCM sees both displays, it'll use LiDisplay.

Q: (Beta) Why do I have to recompile the LiBCM firmware to change parameters?
A: I haven't written the code to do this yet.
A: The beta screen doesn't allow user input (in the future, the LiDisplay touch screen will).
A: The firmware will eventually support real-time configuration (via the LiDisplay touch screen).

Q: How do I power cycle LiBCM?
A: With the key off, turn the IMA switch off, wait five seconds, then turn the IMA switch back on.
OR
A: Plug a USB cable into LiBCM, then open a serial monitor (115200 bps).  This will reset LiBCM unless the "DISABLE RESET" DIP switch is set to 'ON'.
OR
A: Upload new firmware to LiBCM.

Q: Why does the Bay3 BMS connector not have latching tabs (like Bay1 & Bay2)?
A: Safety.  The right angle connectors on Bay1 & Bay2 have exposed conductors on the mating side.  When only Bay1 & Bay2 are plugged in - but not Bay3 - the highest HVDC delta on the PCB is relatively low, whereas when Bay3 is connected, up to 150 VDC can exist on the PCB.
A: This connector shouldn't work its way loose once the LiBCM PCB is installed.  If you have concerns (you shouldn't), then you can drill a 4 mm hole through the left side of the plastic IMA enclosure, then screw an M4x25 bolt into the hole.  Position the hole such that the bolt shaft depth will prevent the ribbon connector from working out (once the PCB is screwed to the enclosure).  Based tens of thousands of miles driven during the beta program, this is not necessary.

Q: (Beta) Why is assist current positive (e.g. +50 A), and regen current negative (e.g. -50 A)?
A: The math is easier this way.
A: The sign will eventually flip to mimic the OEM behavior.  For now flipping the sign confuses me.  

Q: Can I collect data (e.g. with an external laptop)?
A: Yes.  With the key off, plug LiBCM's USB cable into a host computer, then open a 115200 bps serial connection (e.g. using Arduino's Serial Monitor window).

Q: Do you still recommend cutting the DCDC's WHT/GRN wire (to keep 12 volt battery charged)?
A: Yes.  Honda's goal was to slightly improve mpg (by selectively not charging the 12 volt battery).  However, that design decision is a false economy, as it rapidly degrades the 12 volt battery. 
A: Cutting the WHT/GRN wire forces the DCDC to output 14.x volts, which keeps the 12 volt battery charged (just like a traditional alternator does).
A: Cutting the WHT/GRN wire is not required and technically has nothing to do with LiBCM.

Q: Can LiBCM turn the DCDC converter on whenever the key is in the 'ON' position?
A: Yes, by connecting the DCDC's GRN/BLK wire to a GPIO pin on LiBCM.
A: Full details to be announced later.

Q: How does LiBCM calculate battery state-of-charge?
A: When the car is on, LiBCM integrates the measured pack current.  While the car is on, SoC uncertainty increases less than 1% per hour (e.g. after driving the car continuously for 5 hours, the SoC uncertainty is 5%).
A: When the car is off, LiBCM estimates SoC based on the resting cell voltage (to remove accumulated integration error).  Each keyOff event resets the accumulated uncertainty to 0%.
A: You can manually set SoC to any value (via USB interface).  However, LiBCM will automatically adjust SoC based on its own internal knowledge of the battery. For example, if you set the battery size to 1000 mAh, but the battery is actually 5000 mAh, then LiBCM will automatically adjust to the actual value. In that sense, any value you manually enter is just a guideline for LiBCM to start from.

Q: How does LiBCM report state of charge (SoC)?
A: LiBCM's 4x20 Display (and LiDisplay): The actual SoC is shown on the screen, where 0% is a completely empty pack (3.00 volts resting) and 100% is completely full (4.200 volts resting).  LiBCM uses the SoC range between 10% & 85%.
A: OBDIIC&C: The actual SoC is remapped to mimic the OEM NiMH range, which is required to properly apply regen and assist.
A: Instrument Panel: The SoC is not presently displayed on the dashboard gauge.  Instead, the value always remains 'stuck' at a single value (e.g. 19 bars).  A future firmware update should resolve this issue.

Q: What testing is performed on each LiBCM prior to shipping?
A: Each subassembly is 100% function tested using custom hardware.
A: Each cell voltage circuit is measured, both electrically and thermally.
A: Each BMS adapter undergoes a two-stage test procedure to verify there are no shorts, and that each wire is routed to the correct position on both connectors.
A: Each BMS adapter is plugged into a known-good LiBCM, and then the voltages are measured.
A: Each PCB is connected to a simulated Honda Insight IMA system, and then each subsystem is tested using the following code: https://github.com/doppelhub/Honda_Insight_LiBCM/blob/main/Firmware/MVP/BringupTester.cpp
A: Each high current cable undergoes a five second, 100 amp test to verify low cable resistance.
A: Each LCD display is tested using a known-good PCB.
A: Each PCB is 100% visually inspected three times (after SMT, after reflow, and after thru hole).

Q: How "open source" is LiBCM?
A: 100%.  The entire design is located here: github.com/doppelhub/Honda_Insight_LiBCM

Q: Can I manufacture and sell my own LiBCM modules?
A: Yes, except that you cannot use the names 'LiBCM' or 'Linsight'.
A: Full disclosure: you probably won't make any money doing it.

Q: Why doesn't LiBCM support ____________?
A: Maybe it should?  I'm all ears for any and all feature requests.
A: Post all feature requests in the relevant insightcentral.net forums.

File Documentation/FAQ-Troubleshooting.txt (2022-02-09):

Q: I found a problem with the firmware/hardware/LiBCM.  How do I request support?
A: insightcentral.net/threads/libcm-open-beta-support-thread.128957/page-6#post-1495530
OR
A: github.com/doppelhub/Honda_Insight_LiBCM/issues
A: Please include useful troubleshooting information for a quick response.  "It doesn't work" isn't actionable.  A youtube video showing the behavior is strongly encouraged.

Q: I turned the key on while the grid charger was plugged in.  Now I have a P1648 code.  What do I do?
A: To prevent driving off while the grid charger is plugged in, LiBCM does not allow grid charging when the key is on.  If the grid charger is connected and the key is on, LiBCM will:
-emit a continuous audible beep until the key is turned off, and;
-display a warning message on the LCD, and;
-set a Pcode and disable IMA-starting.

Q: Why does LiBCM sometimes emit an audible beep during heavy regenerative braking?
A: (Beta) LiBCM emits an alarm whenever any cell voltage exceeds 4.200 volts.  Future firmware updates will more intelligently limit the maximum cell voltage (based on current amplitude).
A: LiBCM will tell the MCM to disable regen before any cell voltage gets this high, but sometimes the delay is too long and the voltage briefly exceeds 4.200 volts.
A: When the batteries are nearly full, heavy regen can cause the cell voltage to briefly spike above this limit.
A: If the beep stops when you let off the brake pedal, then there's nothing to worry about.
A: If the beeping persists, IMMEDIATE manual user interaction is required (e.g. engage Calpod Switch, place transmission in neutral, etc).
A: Heavy regen produces severe RF noise inside the IMA bay.  Even with heavy analog filtering, this noise electrically couples into the BMS cell voltage measurement circuitry, and can temporarily cause incorrect voltage readings during heavy regen.

Q: How do I update new firmware?
A: (Beta) Watch the "Upload Firmware" video here: linsight.org/install/diy-libcm-kit/libcm-into-car 
A: Make sure the car is off (or you'll get a CEL).
A: The IMA switch can either be off or on (doesn't matter).

Q: While uploading the firmware, why does Arduino sometimes display warning messages?
A: The compiler is trying (in vain) to be helpful.
A: The warnings aren't important... the code still compiles just fine.
A: There won't be any warnings when the firmware hits V1.0.0.

Q: Why can't I upload firmware onto the Arduino Mega PCB when it's disconnected from the LiBCM PCB?
A: Why did you do that?  Put it back together!
A: The Arduino PCB connected to LiBCM has a custom bootloader that prevents host-initiated hardware resets unless both PCBs are mated together.
FYI: The custom bootloader allows LiBCM to boot in just 16.1 ms (the stock bootloader takes 920 ms).  Faster booting prevents P1648-related errors (when LiBCM was initially off and the key turns on).

Q: What are the two DIP switches on the LiBCM PCB used for?
A: "Disable Reset" = ON: plugging in the USB cable does not restart LiBCM, but USB firmware updates are not allowed
A: "Disable Reset" = OFF: plugging in the USB cable restarts LiBCM, and USB firmware updates are allowed (default)
A: "User Switch" is firmware-programmable behavior.  Not presently implemented for any specific task.

Q: How do I troubleshoot a failing lithium cell?
A: A failing cell will tend to charge/discharge faster during regen/assist, respectively.  
A: LiBCM can help you determine if any cells are in worse shape than the rest of the pack.  First, turn the car off and wait for LiBCM to (automatically) balance the cells.  Depending on how unbalanced the pack is, this could take several hours.  Tip: Plug in the grid charger while the key is off to see realtime data on the the LCD.  Once the cells are balanced to less than 1 mV, unplug the grid charger and drive the car until the pack is nearly empty.  If the resting delta grows rapidly (e.g. to more than 15 mV), then it's likely that at least one cell is failing.  You can plug a laptop into the USB cable and see realtime voltage readings for all cells.  Previously balanced cells that quickly develop large voltage deviations (from the pack average) are likely failing.
A:LiBCM's balancing circuitry cannot 'fix' broken cells, but it can prevent cells from under/over-charging, thus prolonging lifetime.

Q: Why won't LiBCM work if the safety cover isn't installed?
A: To prevent you from installing LiBCM into a car without the safety cover installed
A: You can disable this in firmware, if you know what you're doing... but really just install the cover.

Q: After installing LiBCM, my OBDIIC&C keeps resetting.  What's wrong?
A: The longer high current leads inside LiBCM-equipped IMA packs can generate increased RF noise under heavy regen/assist.  This noise can conduct into the H-Line signal.  Honda's H-Line signal is intended to be a debug tool only, and is not used by the vehicle in normal use.  However, the aftermarket OBDIIC&C uses this bus to query data from the various vehicle computers.
A: If your OBDIIC&C resets aftrer installing LiBCM, OBDIIC&C's designer recommends:
	-placing a 10 nF capacitor between H-Line and GND at the OBDIIC&C PCB.
	-adding a 1 kOhm pulling from the H-Line to 5V at the OBDIIC&C PCB.

Q: (18S-/18S-/12S+ only): I forgot to plug in the RED (or BLU) high current connector before using LiBCM.  Did I damage LiBCM?
A: If you only plugged in the grid charger, then LiBCM is probably.
A: If you attempted to drive the car, then you almost certainly damaged LiBCM.
A: Contact Linsight for more information.

Q: The 4x20 LCD backlight turns on, but I don't see any text.  What's wrong?
A: Adjust the potentiometer on the LCD's back side, using a small flathead screwdriver.
A: Turn the key off/on.
A: Verify the 10' cable is plugged in correctly.
A: See: youtube.com/watch?v=vtU__58DWYw

Q: The 4x20 LCD text sometimes gets corrupted while driving.  What's wrong?
A: Users that have reported this issue typically resolve it by moving the LCD cable further away from the harness that travels down the center console (to the IMA bay).
A: The IMA system generates considerable RF noise, which gets coupled into the cables leaving the IMA bay.  Even with massive RF signal filtering, the noise can sometimes corrupt data heading to the 4x20 LCD.
A: The 4x20 LCD uses an archaic 4-bit serial architecture, which lacks any data validation and requires LiBCM to maintain an elaborate state machine (the actual screen is 'modally dumb').  Therefore, when an error occurs, sending the same data again doesn't 'fix' the issue (since LiBCM's state machine now differs from the LCD's).
A: LiBCM cannot 'read back' the data on the 4x20 display... it's a classic "king's messenger" problem: LiBCM cannot sense when errors have occurred, but when they do, LiBCM's state machine doesn't match the 4x20 LCD's, so subsequent data transmissions further corrupt the screen characters.
A: Since LiBCM cannot detect transmission errors to the LCD, it cannot fix them (e.g. by sending the data again).
A: The only way for the LCD to recover from a data corruption is to reset the screen, so that both state machines are in a known-good state.  Unfortunately, resetting the LCD requires LiBCM's full attention (due to the archaic 4-bit architecture, which has specific timing requirements).  Therefore, resetting the LCD isn't possible while the car is running (this would cause a check engine light).  Therefore, LiBCM resets the 4x20 LCD each time the car turns off, so that the screen can recover (until the next transmission error occurs).
A: The 4x20 LCD will go away when the Open Beta period ends.
A: A new touch screen ('LiDisplay') will be released at the same time. It won't suck.

Q: Why do I sometimes get IMA error code P1648 while driving?
A: P1648 means LiBCM isn't sending data to the MCM.
A: If the P1648 error occurs infrequently, then it's probably an RF noise issue.  A beta tester noted that moving the 4x20 LCD cable further away from the main wire harness near the parking brake reduced the error rate.  The production LCD cables are shielded, and there's more signal conditioning on the conductors.  Production LiBCM units probably won't get RF-related P1648 errors.
A: If the P1648 error occurs immediately and persists across several drive cycles, then LiBCM isn't powered, or the firmware isn't running.  Troubleshooting steps:
-Verify the IMA switch is on.
-Turn the IMA switch off and then on.
-Update the firmware
-Check the 5x20mm fuses located on the LiBCM PCB

Q: Why do I sometimes get P1576(12) while driving?
A: P1576(12) occurs when the MCM'E' voltage disagrees with the VPIN voltage by more than 10 volts for more than two seconds.  
A: LiBCM spoofs both of these voltages.  However, in some cars the MCM's HVDC insulation resistance test routine ("Leakage Test") causes an additional (constant) voltage offset to occur, particularly when the pack is fully charged.
A: Adjusting the MCME_VOLTAGE_OFFSET_ADJUST parameter in config.h can fix this issue.
A: Most cars work well with the default '12' volt offset.
A: Some cars require a different offset value.  To calculate this value, turn the car on and drive it until autostop activates.  The IMA light must NOT be on (because the Leakage Test routine is disabled whenever the IMA light is on).  Once autostop activates, record LiBCM's spoofed pack voltage (shown on the 4x20 display).  Next, record the IMA pack voltage observed on the OBDIIC&C.  If these values aren't identical, then you need to increase or decrease the MCME_VOLTAGE_OFFSET_ADJUST value until they are equal.
A: Without an OBDIIC&C, you can "guess and check" different MCME_VOLTAGE_OFFSET_ADJUST values (e.g. 15, 9, 7, 17 volts, etc).  A logical way to do this would be to determine the lower and upper limits that cause an immediate P1576(12), and then calculate the midpoint between those limits.

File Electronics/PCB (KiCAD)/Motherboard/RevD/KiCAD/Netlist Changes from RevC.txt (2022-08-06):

Info: Checking netlist symbol footprint "BZ1:/A4BD9DE2:Linsight:BUZZER_WT-1205".
Info: Checking netlist symbol footprint "C1:/6D38852A:Capacitor_SMD:C_0805_2012Metric".
Info: Checking netlist symbol footprint "C2:/6D2435B0:Capacitor_SMD:C_0805_2012Metric".
Info: Checking netlist symbol footprint "C3:/62A9877F:Capacitor_SMD:C_0805_2012Metric".
Info: Checking netlist symbol footprint "C4:/56B0C3DC:Capacitor_SMD:C_0805_2012Metric".
Info: Checking netlist symbol footprint "C5:/6639E5B1:Capacitor_SMD:C_0805_2012Metric".
Info: Checking netlist symbol footprint "C6:/6639F29F:Capacitor_SMD:C_0805_2012Metric".
Info: Checking netlist symbol footprint "C7:/6639FA04:Capacitor_SMD:C_0805_2012Metric".
Info: Checking netlist symbol footprint "C8:/683FFCE0:Capacitor_SMD:C_1210_3225Metric".
Info: Checking netlist symbol footprint "U16:/645C1173:Package_TO_SOT_SMD:TSOT-23-6".
Info: Checking netlist symbol footprint "C9:/6639FDE3:Capacitor_SMD:C_0805_2012Metric".
Info: Checking netlist symbol footprint "C10:/6A82DAB3:Capacitor_SMD:C_0805_2012Metric".
Info: Checking netlist symbol footprint "C11:/684005E3:Capacitor_SMD:C_0805_2012Metric".
Info: Checking netlist symbol footprint "U15:/5683240B/64E39727:Linsight:LTC6804-2".
Info: Checking netlist symbol footprint "C12:/69E52275:Capacitor_SMD:C_0805_2012Metric".
Info: Checking netlist symbol footprint "C13:/6A0D8749:Capacitor_SMD:C_0805_2012Metric".
Info: Checking netlist symbol footprint "C14:/679EB200:Capacitor_SMD:C_0805_2012Metric".
Info: Checking netlist symbol footprint "U14:/5683240B/724A6428:Linsight:LTC6804-2".
Info: Checking netlist symbol footprint "C15:/568DA56A:Capacitor_SMD:C_0805_2012Metric".
Info: Checking netlist symbol footprint "C16:/6ACFC3F0:Capacitor_SMD:C_0805_2012Metric".
Info: Checking netlist symbol footprint "C17:/68BA869F:Capacitor_SMD:C_1210_3225Metric".
Info: Checking netlist symbol footprint "U13:/5683240B/56892C76:Linsight:LTC6804-2".
Info: Checking netlist symbol footprint "C18:/68A329A6:Capacitor_SMD:C_1210_3225Metric".
Info: Checking netlist symbol footprint "U12:/5683240B/56889A47:Linsight:LTC6804-2".
Info: Checking netlist symbol footprint "C19:/68028D30:Capacitor_SMD:C_1210_3225Metric".
Info: Checking netlist symbol footprint "U11:/5683240B/56833B23:Linsight:LTC6804-2".
Info: Checking netlist symbol footprint "C20:/6DBC3AF3:Capacitor_SMD:CP_Elec_10x10".
Info: Checking netlist symbol footprint "U10:/5683240B/569DB845:Linsight:LTC6820_MSOP".
Info: Checking netlist symbol footprint "C21:/67EFF5B0:Capacitor_SMD:C_0805_2012Metric".
Info: Checking netlist symbol footprint "C22:/65A35F83:Capacitor_SMD:C_0805_2012Metric".
Info: Checking netlist symbol footprint "C23:/56907153:Capacitor_SMD:C_1210_3225Metric".
Info: Checking netlist symbol footprint "C24:/60EF372A:Capacitor_SMD:C_0805_2012Metric".
Info: Checking netlist symbol footprint "C25:/569072C2:Capacitor_SMD:C_1210_3225Metric".
Info: Checking netlist symbol footprint "C26:/56907432:Capacitor_SMD:C_1210_3225Metric".
Info: Checking netlist symbol footprint "U9:/60D82884:Package_DIP:SMDIP-6_W9.53mm".
Info: Checking netlist symbol footprint "C27:/60FBC867:Capacitor_SMD:CP_Elec_10x10".
Info: Checking netlist symbol footprint "C28:/60FBBFAB:Capacitor_SMD:CP_Elec_10x10".
Info: Checking netlist symbol footprint "C29:/65ADBF38:Capacitor_SMD:C_0805_2012Metric".
Info: Checking netlist symbol footprint "C30:/62376A80:Capacitor_THT:CP_Radial_D22.0mm_P10.00mm_SnapIn".
Info: Checking netlist symbol footprint "C31:/61357A07:Capacitor_SMD:C_1206_3216Metric".
Info: Checking netlist symbol footprint "C32:/65C64413:Capacitor_SMD:C_1210_3225Metric".
Info: Checking netlist symbol footprint "U8:/60DB63FF:Linsight:DCDC-EPM1210SJ".
Info: Checking netlist symbol footprint "U7:/606EEE60:Package_DIP:SMDIP-4_W9.53mm_Clearance8mm".
Info: Changing component path "C32:/605DDDFB" to "/65C64413".
Info: Checking netlist symbol footprint "U6:/60C861CB:Package_DIP:SMDIP-4_W9.53mm_Clearance8mm".
Info: Checking netlist symbol footprint "U5:/605BE658:Package_DIP:SMDIP-6_W9.53mm".
Info: Checking netlist symbol footprint "C33:/6074D9E0:Capacitor_SMD:C_1206_3216Metric".
Info: Checking netlist symbol footprint "C34:/5683240B/569DBC36:Capacitor_SMD:C_0805_2012Metric".
Info: Checking netlist symbol footprint "C35:/5683240B/56843C03:Capacitor_SMD:C_0805_2012Metric".
Info: Checking netlist symbol footprint "C36:/5683240B/5684552D:Capacitor_SMD:C_0805_2012Metric".
Info: Checking netlist symbol footprint "C37:/5683240B/56846363:Capacitor_SMD:C_0805_2012Metric".
Info: Checking netlist symbol footprint "C38:/5683240B/568463B9:Capacitor_SMD:C_0805_2012Metric".
Info: Checking netlist symbol footprint "C39:/5683240B/56846FF9:Capacitor_SMD:C_0805_2012Metric".
Info: Checking netlist symbol footprint "C40:/5683240B/5684704F:Capacitor_SMD:C_0805_2012Metric".
Info: Checking netlist symbol footprint "C41:/5683240B/568572C1:Capacitor_SMD:C_0805_2012Metric".
Info: Checking netlist symbol footprint "C42:/5683240B/5684505F:Capacitor_SMD:C_0805_2012Metric".
Info: Checking netlist symbol footprint "C43:/5683240B/56845558:Capacitor_SMD:C_0805_2012Metric".
Info: Checking netlist symbol footprint "C44:/5683240B/5684638E:Capacitor_SMD:C_0805_2012Metric".
Info: Checking netlist symbol footprint "C45:/5683240B/568463E4:Capacitor_SMD:C_0805_2012Metric".
Info: Checking netlist symbol footprint "C46:/5683240B/56847024:Capacitor_SMD:C_0805_2012Metric".
Info: Checking netlist symbol footprint "C47:/5683240B/5684707A:Capacitor_SMD:C_0805_2012Metric".
Info: Checking netlist symbol footprint "C48:/5683240B/569D5707:Capacitor_SMD:C_0805_2012Metric".
Info: Checking netlist symbol footprint "C49:/5683240B/56857ED6:Capacitor_SMD:C_0805_2012Metric".
Info: Checking netlist symbol footprint "C50:/5683240B/699D7919:Capacitor_SMD:C_0805_2012Metric".
Info: Checking netlist symbol footprint "C51:/5683240B/568670ED:Capacitor_SMD:C_0805_2012Metric".
Info: Checking netlist symbol footprint "C52:/5683240B/569C9A15:Capacitor_SMD:C_0805_2012Metric".
Info: Checking netlist symbol footprint "C53:/5683240B/56867A4A:Capacitor_SMD:C_0805_2012Metric".
Info: Checking netlist symbol footprint "C54:/5683240B/56867F46:Capacitor_SMD:C_0805_2012Metric".
Info: Checking netlist symbol footprint "C55:/5683240B/66C36DA5:Capacitor_SMD:C_1206_3216Metric".
Info: Checking netlist symbol footprint "C56:/5683240B/66C3766C:Capacitor_SMD:C_1206_3216Metric".
Info: Checking netlist symbol footprint "C57:/5683240B/568898A2:Capacitor_SMD:C_0805_2012Metric".
Info: Checking netlist symbol footprint "C58:/5683240B/568898E0:Capacitor_SMD:C_0805_2012Metric".
Info: Checking netlist symbol footprint "C59:/5683240B/5688991E:Capacitor_SMD:C_0805_2012Metric".
Info: Checking netlist symbol footprint "C60:/5683240B/5688995C:Capacitor_SMD:C_0805_2012Metric".
Info: Checking netlist symbol footprint "C61:/5683240B/5688999A:Capacitor_SMD:C_0805_2012Metric".
Info: Checking netlist symbol footprint "C62:/5683240B/568899D8:Capacitor_SMD:C_0805_2012Metric".
Info: Checking netlist symbol footprint "C63:/5683240B/56889A0A:Capacitor_SMD:C_0805_2012Metric".
Info: Checking netlist symbol footprint "C64:/5683240B/568898C1:Capacitor_SMD:C_0805_2012Metric".
Info: Checking netlist symbol footprint "C65:/5683240B/568898FF:Capacitor_SMD:C_0805_2012Metric".
Info: Checking netlist symbol footprint "C66:/5683240B/5688993D:Capacitor_SMD:C_0805_2012Metric".
Info: Checking netlist symbol footprint "C67:/5683240B/5688997B:Capacitor_SMD:C_0805_2012Metric".
Info: Checking netlist symbol footprint "C68:/5683240B/568899B9:Capacitor_SMD:C_0805_2012Metric".
Info: Checking netlist symbol footprint "C69:/5683240B/568899F7:Capacitor_SMD:C_0805_2012Metric".
Info: Checking netlist symbol footprint "C70:/5683240B/56889A16:Capacitor_SMD:C_0805_2012Metric".
Info: Checking netlist symbol footprint "C71:/5683240B/7ECE4682:Capacitor_SMD:C_1206_3216Metric".
Info: Checking netlist symbol footprint "C72:/5683240B/7ECE467C:Capacitor_SMD:C_1206_3216Metric".
Info: Checking netlist symbol footprint "C73:/5683240B/698AE82E:Capacitor_SMD:C_0805_2012Metric".
Info: Checking netlist symbol footprint "C74:/5683240B/56889A35:Capacitor_SMD:C_0805_2012Metric".
Info: Checking netlist symbol footprint "C75:/5683240B/56889A3B:Capacitor_SMD:C_0805_2012Metric".
Info: Checking netlist symbol footprint "C76:/5683240B/56889A41:Capacitor_SMD:C_0805_2012Metric".
Info: Checking netlist symbol footprint "C77:/5683240B/7ECE4676:Capacitor_SMD:C_0805_2012Metric".
Info: Checking netlist symbol footprint "C78:/5683240B/7F1C7FF3:Capacitor_SMD:C_1206_3216Metric".
Info: Checking netlist symbol footprint "C79:/5683240B/56892AD1:Capacitor_SMD:C_0805_2012Metric".
Info: Checking netlist symbol footprint "C80:/5683240B/56892B0F:Capacitor_SMD:C_0805_2012Metric".
Info: Checking netlist symbol footprint "C81:/5683240B/56892B4D:Capacitor_SMD:C_0805_2012Metric".
Info: Checking netlist symbol footprint "C82:/5683240B/56892B8B:Capacitor_SMD:C_0805_2012Metric".
Info: Checking netlist symbol footprint "C83:/5683240B/56892BC9:Capacitor_SMD:C_0805_2012Metric".
Info: Checking netlist symbol footprint "C84:/5683240B/56892C07:Capacitor_SMD:C_0805_2012Metric".
Info: Checking netlist symbol footprint "C85:/5683240B/56892C39:Capacitor_SMD:C_0805_2012Metric".
Info: Checking netlist symbol footprint "C86:/5683240B/56892AF0:Capacitor_SMD:C_0805_2012Metric".
Info: Checking netlist symbol footprint "C87:/5683240B/56892B2E:Capacitor_SMD:C_0805_2012Metric".
Info: Checking netlist symbol footprint "C88:/5683240B/56892B6C:Capacitor_SMD:C_0805_2012Metric".
Info: Checking netlist symbol footprint "C89:/5683240B/56892BAA:Capacitor_SMD:C_0805_2012Metric".
Info: Checking netlist symbol footprint "C90:/5683240B/56892BE8:Capacitor_SMD:C_0805_2012Metric".
Info: Checking netlist symbol footprint "C91:/5683240B/56892C26:Capacitor_SMD:C_0805_2012Metric".
Info: Checking netlist symbol footprint "C92:/5683240B/7F1C7FED:Capacitor_SMD:C_1206_3216Metric".
Info: Checking netlist symbol footprint "C93:/5683240B/7F1C7FE7:Capacitor_SMD:C_0805_2012Metric".
Info: Checking netlist symbol footprint "C94:/5683240B/56892C45:Capacitor_SMD:C_0805_2012Metric".
Info: Checking netlist symbol footprint "C95:/5683240B/7F444B07:Capacitor_SMD:C_1206_3216Metric".
Info: Checking netlist symbol footprint "C96:/5683240B/7F444B01:Capacitor_SMD:C_1206_3216Metric".
Info: Checking netlist symbol footprint "C97:/5683240B/69FAA7DC:Capacitor_SMD:C_0805_2012Metric".
Info: Checking netlist symbol footprint "C98:/5683240B/56892C64:Capacitor_SMD:C_0805_2012Metric".
Info: Checking netlist symbol footprint "C99:/5683240B/56892C6A:Capacitor_SMD:C_0805_2012Metric".
Info: Checking netlist symbol footprint "C100:/5683240B/56892C70:Capacitor_SMD:C_0805_2012Metric".
Info: Checking netlist symbol footprint "C101:/79C53C47:Capacitor_SMD:C_0805_2012Metric".
Info: Checking netlist symbol footprint "C102:/79C53C4D:Capacitor_SMD:C_0805_2012Metric".
Info: Checking netlist symbol footprint "C103:/5683240B/7F444AFB:Capacitor_SMD:C_0805_2012Metric".
Info: Checking netlist symbol footprint "C104:/5683240B/724A6295:Capacitor_SMD:C_0805_2012Metric".
Info: Checking netlist symbol footprint "C105:/5683240B/724A62D3:Capacitor_SMD:C_0805_2012Metric".
Info: Checking netlist symbol footprint "C106:/5683240B/724A6311:Capacitor_SMD:C_0805_2012Metric".
Info: Checking netlist symbol footprint "C107:/5683240B/724A634F:Capacitor_SMD:C_0805_2012Metric".
Info: Checking netlist symbol footprint "C108:/5683240B/724A638D:Capacitor_SMD:C_0805_2012Metric".
Info: Checking netlist symbol footprint "C109:/5683240B/724A63CB:Capacitor_SMD:C_0805_2012Metric".
Info: Checking netlist symbol footprint "C110:/5683240B/724A63FD:Capacitor_SMD:C_0805_2012Metric".
Info: Checking netlist symbol footprint "C111:/5683240B/724A62B4:Capacitor_SMD:C_0805_2012Metric".
Info: Checking netlist symbol footprint "C112:/5683240B/724A62F2:Capacitor_SMD:C_0805_2012Metric".
Info: Checking netlist symbol footprint "C113:/5683240B/724A6330:Capacitor_SMD:C_0805_2012Metric".
Info: Checking netlist symbol footprint "C114:/5683240B/724A636E:Capacitor_SMD:C_0805_2012Metric".
Info: Checking netlist symbol footprint "C115:/5683240B/724A63AC:Capacitor_SMD:C_0805_2012Metric".
Info: Checking netlist symbol footprint "C116:/5683240B/724A63EA:Capacitor_SMD:C_0805_2012Metric".
Info: Checking netlist symbol footprint "C117:/5683240B/724A663C:Capacitor_SMD:C_0805_2012Metric".
Info: Checking netlist symbol footprint "C118:/5683240B/724A6649:Capacitor_SMD:C_0805_2012Metric".
Info: Checking netlist symbol footprint "C119:/5683240B/724A6416:Capacitor_SMD:C_0805_2012Metric".
Info: Checking netlist symbol footprint "C120:/5683240B/724A641C:Capacitor_SMD:C_0805_2012Metric".
Info: Checking netlist symbol footprint "C121:/5683240B/724A6422:Capacitor_SMD:C_0805_2012Metric".
Info: Checking netlist symbol footprint "C122:/5683240B/64E39594:Capacitor_SMD:C_0805_2012Metric".
Info: Checking netlist symbol footprint "C123:/5683240B/64E395D2:Capacitor_SMD:C_0805_2012Metric".
Info: Checking netlist symbol footprint "C124:/5683240B/64E39610:Capacitor_SMD:C_0805_2012Metric".
Info: Checking netlist symbol footprint "C125:/5683240B/64E3964E:Capacitor_SMD:C_0805_2012Metric".
Info: Checking netlist symbol footprint "C126:/5683240B/64E3968C:Capacitor_SMD:C_0805_2012Metric".
Info: Checking netlist symbol footprint "C127:/5683240B/64E396CA:Capacitor_SMD:C_0805_2012Metric".
Info: Checking netlist symbol footprint "C128:/5683240B/64E396FC:Capacitor_SMD:C_0805_2012Metric".
Info: Checking netlist symbol footprint "C129:/5683240B/64E395B3:Capacitor_SMD:C_0805_2012Metric".
Info: Checking netlist symbol footprint "C130:/5683240B/64E395F1:Capacitor_SMD:C_0805_2012Metric".
Info: Checking netlist symbol footprint "C131:/5683240B/64E3962F:Capacitor_SMD:C_0805_2012Metric".
Info: Checking netlist symbol footprint "C132:/5683240B/64E3966D:Capacitor_SMD:C_0805_2012Metric".
Info: Checking netlist symbol footprint "C133:/5683240B/64E396AB:Capacitor_SMD:C_0805_2012Metric".
Info: Checking netlist symbol footprint "C134:/5683240B/64E396E9:Capacitor_SMD:C_0805_2012Metric".
Info: Checking netlist symbol footprint "C135:/5683240B/64E398E4:Capacitor_SMD:C_0805_2012Metric".
Info: Checking netlist symbol footprint "C136:/5683240B/64E398EB:Capacitor_SMD:C_0805_2012Metric".
Info: Checking netlist symbol footprint "C137:/5683240B/64E39715:Capacitor_SMD:C_0805_2012Metric".
Info: Checking netlist symbol footprint "C138:/5683240B/64E3971B:Capacitor_SMD:C_0805_2012Metric".
Info: Checking netlist symbol footprint "C139:/5683240B/64E39721:Capacitor_SMD:C_0805_2012Metric".
Info: Checking netlist symbol footprint "C140:/5683240B/67F39621:Capacitor_SMD:C_1206_3216Metric".
Info: Checking netlist symbol footprint "C141:/5683240B/67F39CBA:Capacitor_SMD:C_1206_3216Metric".
Info: Checking netlist symbol footprint "C142:/5683240B/6742BEFA:Capacitor_SMD:C_0805_2012Metric".
Info: Checking netlist symbol footprint "C143:/777C74BD:Capacitor_SMD:C_1210_3225Metric".
Info: Checking netlist symbol footprint "U4:/659C6C7A:Package_TO_SOT_SMD:TSOT-23-5".
Info: Checking netlist symbol footprint "C144:/61566EDF:Capacitor_SMD:C_0805_2012Metric".
Info: Checking netlist symbol footprint "C145:/74A5FE12:Capacitor_SMD:C_0805_2012Metric".
Info: Checking netlist symbol footprint "U3:/6ACFC3DC:Package_SO:SOIC-8_3.9x4.9mm_P1.27mm".
Info: Checking netlist symbol footprint "U2:/568D08A5:Package_SO:SOIC-8_3.9x4.9mm_P1.27mm".
Info: Changing component path "U1:/61F9F4FF" to "/645CA810".
Info: Checking netlist symbol footprint "C146:/6403B8C8:Capacitor_SMD:C_1210_3225Metric".
Info: Checking netlist symbol footprint "C147:/63B84612:Capacitor_SMD:C_0805_2012Metric".
Info: Checking netlist symbol footprint "C148:/636DEC9C:Capacitor_SMD:C_1206_3216Metric".
Info: Checking netlist symbol footprint "C149:/63B8588F:Capacitor_SMD:C_0805_2012Metric".
Info: Checking netlist symbol footprint "C150:/63637A86:Capacitor_SMD:C_1206_3216Metric".
Info: Checking netlist symbol footprint "C151:/62DDB36F:Capacitor_SMD:C_1206_3216Metric".
Info: Checking netlist symbol footprint "C152:/62D3835F:Capacitor_SMD:C_1206_3216Metric".
Info: Checking netlist symbol footprint "C153:/62C964DF:Capacitor_SMD:C_1206_3216Metric".
Info: Checking netlist symbol footprint "C154:/62BF470E:Capacitor_SMD:C_1206_3216Metric".
Info: Checking netlist symbol footprint "C155:/79C53C53:Capacitor_SMD:C_0805_2012Metric".
Info: Checking netlist symbol footprint "C156:/7E4CFBD3:Capacitor_SMD:C_0805_2012Metric".
Info: Checking netlist symbol footprint "C157:/7E4CFBD9:Capacitor_SMD:C_0805_2012Metric".
Info: Checking netlist symbol footprint "C158:/7E4CFBDF:Capacitor_SMD:C_0805_2012Metric".
Info: Checking netlist symbol footprint "C159:/9504C540:Capacitor_SMD:C_0805_2012Metric".
Info: Checking netlist symbol footprint "C160:/95943D2D:Capacitor_SMD:C_0805_2012Metric".
Info: Checking netlist symbol footprint "C161:/9DDBD91C:Capacitor_SMD:C_0805_2012Metric".
Info: Checking netlist symbol footprint "C162:/9E440EC2:Capacitor_SMD:C_0805_2012Metric".
Info: Checking netlist symbol footprint "C163:/9DAF0CA9:Capacitor_SMD:C_0805_2012Metric".
Info: Checking netlist symbol footprint "C164:/7E0947F8:Capacitor_SMD:C_0805_2012Metric".
Info: Checking netlist symbol footprint "C165:/65AFE69B:Capacitor_SMD:C_0805_2012Metric".
Info: Checking netlist symbol footprint "C166:/7E0947FE:Capacitor_SMD:C_0805_2012Metric".
Info: Checking netlist symbol footprint "C167:/7E094804:Capacitor_SMD:C_0805_2012Metric".
Info: Checking netlist symbol footprint "C168:/7E09480A:Capacitor_SMD:C_0805_2012Metric".
Info: Checking netlist symbol footprint "C169:/6E4F7A18:Capacitor_SMD:C_0805_2012Metric".
Info: Checking netlist symbol footprint "C170:/87A5D9B6:Capacitor_SMD:C_0805_2012Metric".
Info: Checking netlist symbol footprint "U1:/645CA810:Package_TO_SOT_SMD:TSOT-23-6".
Info: Checking netlist symbol footprint "C171:/88753105:Capacitor_SMD:C_0805_2012Metric".
Info: Checking netlist symbol footprint "TH5:/5683240B/64E39890:Resistor_SMD:R_0805_2012Metric".
Info: Checking netlist symbol footprint "C172:/5683240B/65C6BE6A:Capacitor_SMD:C_0805_2012Metric".
Info: Checking netlist symbol footprint "C173:/5683240B/8B2DE21A:Capacitor_SMD:C_0805_2012Metric".
Info: Checking netlist symbol footprint "C174:/5683240B/A306A521:Capacitor_SMD:C_0805_2012Metric".
Info: Checking netlist symbol footprint "C175:/5683240B/A34898CF:Capacitor_SMD:C_0805_2012Metric".
Info: Checking netlist symbol footprint "C176:/633B7991:Capacitor_SMD:C_0805_2012Metric".
Info: Checking netlist symbol footprint "TH4:/5683240B/724A65CD:Resistor_SMD:R_0805_2012Metric".
Info: Checking netlist symbol footprint "C177:/5683240B/A3CE28F7:Capacitor_SMD:C_0805_2012Metric".
Info: Checking netlist symbol footprint "C178:/62F49DAF:Capacitor_SMD:C_0805_2012Metric".
Info: Checking netlist symbol footprint "TH3:/5683240B/56A92D9D:Resistor_SMD:R_0805_2012Metric".
Info: Checking netlist symbol footprint "C179:/65C64419:Capacitor_SMD:C_0805_2012Metric".
Info: Checking netlist symbol footprint "TH2:/5683240B/56A908D9:Resistor_SMD:R_0805_2012Metric".
Info: Checking netlist symbol footprint "C180:/64375AF0:Capacitor_SMD:C_0805_2012Metric".
Info: Checking netlist symbol footprint "TH1:/5683240B/56A891E0:Resistor_SMD:R_0805_2012Metric".
Info: Checking netlist symbol footprint "C181:/6611A1AF:Capacitor_SMD:C_0805_2012Metric".
Info: Checking netlist symbol footprint "T3:/5683240B/8105741C:Linsight:Trans_7490100111A".
Info: Checking netlist symbol footprint "C182:/66BF94A3:Capacitor_SMD:C_0805_2012Metric".
Info: Checking netlist symbol footprint "T2:/5683240B/569A73D0:Linsight:Trans_7490100111A".
Info: Checking netlist symbol footprint "C183:/6611A1E7:Capacitor_SMD:C_1210_3225Metric".
Info: Checking netlist symbol footprint "T1:/5683240B/569A76FF:Linsight:Trans_7490100111A".
Info: Checking netlist symbol footprint "C184:/6611A1DB:Capacitor_SMD:C_1210_3225Metric".
Info: Checking netlist symbol footprint "SW2:/615C8130:Button_Switch_SMD:SW_DIP_SPSTx02_Slide_9.78x7.26mm_W8.61mm_P2.54mm".
Info: Checking netlist symbol footprint "C185:/6611A1C8:Capacitor_SMD:C_1210_3225Metric".
Info: Checking netlist symbol footprint "SW1:/79A76AA8:Button_Switch_Keyboard:SW_Cherry_MX_1.00u_PCB".
Info: Checking netlist symbol footprint "C186:/6611A1F9:Capacitor_SMD:C_1210_3225Metric".
Info: Checking netlist symbol footprint "R363:/687FF6CB:Resistor_SMD:R_0805_2012Metric".
Info: Checking netlist symbol footprint "C187:/70A30EDD:Capacitor_SMD:C_1206_3216Metric".
Info: Checking netlist symbol footprint "R362:/66BFD0D5:Resistor_SMD:R_0805_2012Metric".
Info: Checking netlist symbol footprint "C188:/70A30A57:Capacitor_SMD:C_1206_3216Metric".
Info: Checking netlist symbol footprint "R361:/6793B68E:Resistor_SMD:R_0805_2012Metric".
Info: Checking netlist symbol footprint "D1:/69504DD5:LED_SMD:LED_0805_2012Metric_Castellated".
Info: Checking netlist symbol footprint "D2:/6950716D:LED_SMD:LED_0805_2012Metric_Castellated".
Info: Checking netlist symbol footprint "D3:/695066DC:LED_SMD:LED_0805_2012Metric_Castellated".
Info: Checking netlist symbol footprint "D4:/6950785B:LED_SMD:LED_0805_2012Metric_Castellated".
Info: Checking netlist symbol footprint "D5:/68CA5560:Diode_SMD:D_SOD-123".
Info: Checking netlist symbol footprint "D6:/61171C0B:Package_TO_SOT_SMD:TO-263-3_TabPin2".
Info: Checking netlist symbol footprint "R360:/66BFE7C0:Resistor_SMD:R_0805_2012Metric".
Info: Checking netlist symbol footprint "D7:/5683240B/883EB5AB:LED_SMD:LED_0805_2012Metric_Castellated".
Info: Checking netlist symbol footprint "D8:/5683240B/8B1C6F53:LED_SMD:LED_0805_2012Metric_Castellated".
Info: Checking netlist symbol footprint "D9:/5683240B/8BB7BEF3:LED_SMD:LED_0805_2012Metric_Castellated".
Info: Checking netlist symbol footprint "D10:/5683240B/8BDE7AFA:LED_SMD:LED_0805_2012Metric_Castellated".
Info: Checking netlist symbol footprint "D11:/60C8B252:Diode_SMD:D_SOD-123".
Info: Checking netlist symbol footprint "D12:/60C8E6C2:Diode_SMD:D_SOD-123".
Info: Checking netlist symbol footprint "D13:/6113497A:Diode_SMD:D_SOD-123".
Info: Checking netlist symbol footprint "R359:/5683240B/61A07E3A:Resistor_SMD:R_0805_2012Metric".
Info: Checking netlist symbol footprint "D14:/60B149E7:LED_SMD:LED_0805_2012Metric_Castellated".
Info: Checking netlist symbol footprint "D15:/60B15E17:LED_SMD:LED_0805_2012Metric_Castellated".
Info: Checking netlist symbol footprint "D16:/A51F4A2B:Diode_SMD:D_SOD-123".
Info: Checking netlist symbol footprint "D17:/5683240B/64E39A15:LED_SMD:LED_0805_2012Metric_Castellated".
Info: Checking netlist symbol footprint "D18:/A48C2C04:Diode_SMD:D_SMC".
Info: Checking netlist symbol footprint "R358:/7F2E00BE:Resistor_SMD:R_0805_2012Metric".
Info: Checking netlist symbol footprint "F1:/60C6FFF7:Fuse:Fuseholder_Cylinder-5x20mm_Schurter_0031_8201_Horizontal_Open".
Info: Checking netlist symbol footprint "F2:/60C99702:Fuse:Fuseholder_Cylinder-5x20mm_Schurter_0031_8201_Horizontal_Open".
Info: Checking netlist symbol footprint "H1:/610AF96A:MountingHole:MountingHole_6mm_Pad".
Info: Checking netlist symbol footprint "H2:/610AF64E:MountingHole:MountingHole_6mm_Pad".
Info: Checking netlist symbol footprint "H4:/610AF153:MountingHole:MountingHole_6mm_Pad".
Info: Checking netlist symbol footprint "H5:/60FF7EC0:MountingHole:MountingHole_6mm_Pad".
Info: Checking netlist symbol footprint "H6:/610AEACF:MountingHole:MountingHole_6mm_Pad".
Info: Checking netlist symbol footprint "H7:/610AEEC2:MountingHole:MountingHole_6mm_Pad".
Info: Checking netlist symbol footprint "H9:/753D0841:MountingHole:MountingHole_3mm".
Info: Checking netlist symbol footprint "HS1:/70642DD4:Linsight:Heatsink 573300D00010G".
Info: Checking netlist symbol footprint "R357:/5683240B/A3CE2905:Resistor_SMD:R_0805_2012Metric".
Info: Checking netlist symbol footprint "J1:/6396C524:Connector_PinHeader_2.54mm:PinHeader_1x08_P2.54mm_Vertical".
Info: Checking netlist symbol footprint "J2:/864A8F47:Connector_PinHeader_2.54mm:PinHeader_1x08_P2.54mm_Vertical".
Info: Checking netlist symbol footprint "J3:/864F3BB6:Connector_PinHeader_2.54mm:PinHeader_1x08_P2.54mm_Vertical".
Info: Checking netlist symbol footprint "J4:/628A0E07:Connector_PinHeader_2.54mm:PinHeader_2x08_P2.54mm_Vertical".
Info: Checking netlist symbol footprint "J5:/86545B3E:Connector_PinHeader_2.54mm:PinHeader_1x08_P2.54mm_Vertical".
Info: Checking netlist symbol footprint "J6:/86545B38:Connector_PinHeader_2.54mm:PinHeader_1x08_P2.54mm_Vertical".
Info: Checking netlist symbol footprint "J7:/86545B32:Connector_PinHeader_2.54mm:PinHeader_1x08_P2.54mm_Vertical".
Info: Checking netlist symbol footprint "J8:/AA45B031:Connector_PinHeader_2.54mm:PinHeader_1x04_P2.54mm_Vertical".
Info: Checking netlist symbol footprint "J9:/6396A5D2:Linsight:CONN_1751303".
Info: Checking netlist symbol footprint "R356:/5683240B/7DBE1DD6:Resistor_SMD:R_0805_2012Metric".
Info: Checking netlist symbol footprint "R355:/5683240B/7DBE18B3:Resistor_SMD:R_0805_2012Metric".
Info: Checking netlist symbol footprint "R354:/5683240B/7DBE09D6:Resistor_SMD:R_0805_2012Metric".
Info: Checking netlist symbol footprint "J10:/6233278F:Connector_Wire:SolderWire-1sqmm_1x01_D1.4mm_OD2.7mm".
Info: Checking netlist symbol footprint "J11:/609DCD45:Linsight:CONN_1751303".
Info: Checking netlist symbol footprint "J12:/807957C3:Linsight:CONN_WM26831CT-ND".
Info: Checking netlist symbol footprint "J13:/5683240B/60FD5054:Connector_PinHeader_2.54mm:PinHeader_2x10_P2.54mm_Vertical".
Info: Checking netlist symbol footprint "J14:/6219D177:Connector_PinSocket_2.54mm:PinSocket_1x04_P2.54mm_Horizontal".
Info: Checking netlist symbol footprint "J15:/62BD6920:Connector_PinHeader_2.54mm:PinHeader_1x02_P2.54mm_Vertical".
Info: Checking netlist symbol footprint "J16:/5683240B/60FDCF82:Connector_PinHeader_2.54mm:PinHeader_2x10_P2.54mm_Vertical".
Info: Checking netlist symbol footprint "J17:/5683240B/60FECDD3:Connector_PinHeader_2.54mm:PinHeader_2x07_P2.54mm_Vertical".
Info: Checking netlist symbol footprint "J18:/5683240B/60FF4D07:Connector_PinHeader_2.54mm:PinHeader_2x07_P2.54mm_Vertical".
Info: Checking netlist symbol footprint "J19:/811960DB:Linsight:CONN_WM26831CT-ND".
Info: Checking netlist symbol footprint "J20:/812B0D62:Linsight:CONN_WM26831CT-ND".
Info: Checking netlist symbol footprint "J21:/680AAE2F:Connector_PinHeader_2.54mm:PinHeader_1x04_P2.54mm_Vertical".
Info: Checking netlist symbol footprint "J22:/AA8900BB:Connector_PinSocket_2.54mm:PinSocket_1x08_P2.54mm_Vertical".
Info: Checking netlist symbol footprint "L1:/5690D744:Inductor_SMD:L_TDK_SLF7045".
Info: Checking netlist symbol footprint "R353:/5683240B/6DF54310:Resistor_SMD:R_0805_2012Metric".
Info: Checking netlist symbol footprint "L2:/64037351:Inductor_SMD:L_0805_2012Metric".
Info: Checking netlist symbol footprint "L3:/6403B0C4:Inductor_SMD:L_0805_2012Metric".
Info: Checking netlist symbol footprint "L4:/665F374E:Linsight:Inductor_CLF6045NI".
Info: Checking netlist symbol footprint "R352:/5683240B/6DF5430A:Resistor_SMD:R_0805_2012Metric".
Info: Checking netlist symbol footprint "M1:/611AC7FB:Linsight:FAN_60x60OD_50x50Holes".
Info: Checking netlist symbol footprint "M2:/611A91FB:Linsight:FAN_60x60OD_50x50Holes".
Info: Checking netlist symbol footprint "M3:/6139CE84:Linsight:FAN_60x60OD_50x50Holes".
Info: Checking netlist symbol footprint "P1:/6397020C:Linsight:CONN_BCM_174917-6".
Info: Checking netlist symbol footprint "P2:/6396863E:Connector_Wire:SolderWire-1sqmm_1x03_P5.4mm_D1.4mm_OD2.7mm".
Info: Checking netlist symbol footprint "Q1:/61A33DD7:Package_TO_SOT_SMD:SOT-23".
Info: Checking netlist symbol footprint "Q2:/61A32820:Package_TO_SOT_SMD:SOT-23".
Info: Checking netlist symbol footprint "Q3:/754A45AB:Package_TO_SOT_SMD:SOT-23".
Info: Checking netlist symbol footprint "Q4:/61A36935:Package_TO_SOT_SMD:SOT-23".
Info: Checking netlist symbol footprint "Q5:/61A3610E:Package_TO_SOT_SMD:SOT-23".
Info: Checking netlist symbol footprint "Q6:/61A34E44:Package_TO_SOT_SMD:SOT-23".
Info: Checking netlist symbol footprint "Q7:/61832AD1:Package_TO_SOT_SMD:SOT-23".
Info: Checking netlist symbol footprint "Q8:/5683240B/5684410F:Package_TO_SOT_SMD:SOT-23".
Info: Checking netlist symbol footprint "Q9:/5683240B/56845066:Package_TO_SOT_SMD:SOT-23".
Info: Checking netlist symbol footprint "Q10:/5683240B/56845534:Package_TO_SOT_SMD:SOT-23".
Info: Checking netlist symbol footprint "Q11:/5683240B/5684555F:Package_TO_SOT_SMD:SOT-23".
Info: Checking netlist symbol footprint "Q12:/5683240B/5684636A:Package_TO_SOT_SMD:SOT-23".
Info: Checking netlist symbol footprint "Q13:/5683240B/56846395:Package_TO_SOT_SMD:SOT-23".
Info: Checking netlist symbol footprint "Q14:/5683240B/568463C0:Package_TO_SOT_SMD:SOT-23".
Info: Checking netlist symbol footprint "Q15:/5683240B/568463EB:Package_TO_SOT_SMD:SOT-23".
Info: Checking netlist symbol footprint "Q16:/5683240B/56847000:Package_TO_SOT_SMD:SOT-23".
Info: Checking netlist symbol footprint "Q17:/5683240B/5684702B:Package_TO_SOT_SMD:SOT-23".
Info: Checking netlist symbol footprint "Q18:/5683240B/56847056:Package_TO_SOT_SMD:SOT-23".
Info: Checking netlist symbol footprint "Q19:/5683240B/56847081:Package_TO_SOT_SMD:SOT-23".
Info: Checking netlist symbol footprint "Q20:/5683240B/56863A7B:Package_TO_SOT_SMD:SOT-223".
Info: Checking netlist symbol footprint "Q21:/5683240B/568898A9:Package_TO_SOT_SMD:SOT-23".
Info: Checking netlist symbol footprint "Q22:/5683240B/568898C8:Package_TO_SOT_SMD:SOT-23".
Info: Checking netlist symbol footprint "Q23:/5683240B/568898E7:Package_TO_SOT_SMD:SOT-23".
Info: Checking netlist symbol footprint "Q24:/5683240B/56889906:Package_TO_SOT_SMD:SOT-23".
Info: Checking netlist symbol footprint "Q25:/5683240B/56889925:Package_TO_SOT_SMD:SOT-23".
Info: Checking netlist symbol footprint "Q26:/5683240B/56889944:Package_TO_SOT_SMD:SOT-23".
Info: Checking netlist symbol footprint "Q27:/5683240B/56889963:Package_TO_SOT_SMD:SOT-23".
Info: Checking netlist symbol footprint "Q28:/5683240B/56889982:Package_TO_SOT_SMD:SOT-23".
Info: Checking netlist symbol footprint "Q29:/5683240B/568899A1:Package_TO_SOT_SMD:SOT-23".
Info: Checking netlist symbol footprint "Q30:/5683240B/568899C0:Package_TO_SOT_SMD:SOT-23".
Info: Checking netlist symbol footprint "Q31:/5683240B/568899DF:Package_TO_SOT_SMD:SOT-23".
Info: Checking netlist symbol footprint "Q32:/5683240B/568899FE:Package_TO_SOT_SMD:SOT-23".
Info: Checking netlist symbol footprint "Q33:/5683240B/56889A2F:Package_TO_SOT_SMD:SOT-223".
Info: Checking netlist symbol footprint "Q34:/5683240B/56892AD8:Package_TO_SOT_SMD:SOT-23".
Info: Checking netlist symbol footprint "Q35:/5683240B/56892AF7:Package_TO_SOT_SMD:SOT-23".
Info: Checking netlist symbol footprint "Q36:/5683240B/56892B16:Package_TO_SOT_SMD:SOT-23".
Info: Checking netlist symbol footprint "Q37:/5683240B/56892B35:Package_TO_SOT_SMD:SOT-23".
Info: Checking netlist symbol footprint "Q38:/5683240B/56892B54:Package_TO_SOT_SMD:SOT-23".
Info: Checking netlist symbol footprint "Q39:/5683240B/56892B73:Package_TO_SOT_SMD:SOT-23".
Info: Checking netlist symbol footprint "Q40:/5683240B/56892B92:Package_TO_SOT_SMD:SOT-23".
Info: Checking netlist symbol footprint "Q41:/5683240B/56892BB1:Package_TO_SOT_SMD:SOT-23".
Info: Checking netlist symbol footprint "Q42:/5683240B/56892BD0:Package_TO_SOT_SMD:SOT-23".
Info: Checking netlist symbol footprint "Q43:/5683240B/56892BEF:Package_TO_SOT_SMD:SOT-23".
Info: Checking netlist symbol footprint "Q44:/5683240B/56892C0E:Package_TO_SOT_SMD:SOT-23".
Info: Checking netlist symbol footprint "Q45:/5683240B/56892C2D:Package_TO_SOT_SMD:SOT-23".
Info: Checking netlist symbol footprint "Q46:/5683240B/56892C5E:Package_TO_SOT_SMD:SOT-223".
Info: Checking netlist symbol footprint "Q47:/5683240B/724A629C:Package_TO_SOT_SMD:SOT-23".
Info: Checking netlist symbol footprint "Q48:/5683240B/724A62BB:Package_TO_SOT_SMD:SOT-23".
Info: Checking netlist symbol footprint "Q49:/5683240B/724A62DA:Package_TO_SOT_SMD:SOT-23".
Info: Checking netlist symbol footprint "Q50:/5683240B/724A62F9:Package_TO_SOT_SMD:SOT-23".
Info: Checking netlist symbol footprint "Q51:/5683240B/724A6318:Package_TO_SOT_SMD:SOT-23".
Info: Checking netlist symbol footprint "Q52:/5683240B/724A6337:Package_TO_SOT_SMD:SOT-23".
Info: Checking netlist symbol footprint "Q53:/5683240B/724A6356:Package_TO_SOT_SMD:SOT-23".
Info: Checking netlist symbol footprint "Q54:/5683240B/724A6375:Package_TO_SOT_SMD:SOT-23".
Info: Checking netlist symbol footprint "Q55:/5683240B/724A6394:Package_TO_SOT_SMD:SOT-23".
Info: Checking netlist symbol footprint "Q56:/5683240B/724A63B3:Package_TO_SOT_SMD:SOT-23".
Info: Checking netlist symbol footprint "Q57:/5683240B/724A63D2:Package_TO_SOT_SMD:SOT-23".
Info: Checking netlist symbol footprint "Q58:/5683240B/724A63F1:Package_TO_SOT_SMD:SOT-23".
Info: Checking netlist symbol footprint "Q59:/5683240B/724A6410:Package_TO_SOT_SMD:SOT-223".
Info: Checking netlist symbol footprint "Q60:/5683240B/64E3959B:Package_TO_SOT_SMD:SOT-23".
Info: Checking netlist symbol footprint "Q61:/5683240B/64E395BA:Package_TO_SOT_SMD:SOT-23".
Info: Checking netlist symbol footprint "Q62:/5683240B/64E395D9:Package_TO_SOT_SMD:SOT-23".
Info: Checking netlist symbol footprint "Q63:/5683240B/64E395F8:Package_TO_SOT_SMD:SOT-23".
Info: Checking netlist symbol footprint "Q64:/5683240B/64E39617:Package_TO_SOT_SMD:SOT-23".
Info: Checking netlist symbol footprint "Q65:/5683240B/64E39636:Package_TO_SOT_SMD:SOT-23".
Info: Checking netlist symbol footprint "Q66:/5683240B/64E39655:Package_TO_SOT_SMD:SOT-23".
Info: Checking netlist symbol footprint "Q67:/5683240B/64E39674:Package_TO_SOT_SMD:SOT-23".
Info: Checking netlist symbol footprint "Q68:/5683240B/64E39693:Package_TO_SOT_SMD:SOT-23".
Info: Checking netlist symbol footprint "Q69:/5683240B/64E396B2:Package_TO_SOT_SMD:SOT-23".
Info: Checking netlist symbol footprint "Q70:/5683240B/64E396D1:Package_TO_SOT_SMD:SOT-23".
Info: Checking netlist symbol footprint "Q71:/5683240B/64E396F0:Package_TO_SOT_SMD:SOT-23".
Info: Checking netlist symbol footprint "Q72:/5683240B/64E3970F:Package_TO_SOT_SMD:SOT-223".
Info: Checking netlist symbol footprint "Q73:/A55174A2:Package_TO_SOT_SMD:SOT-23".
Info: Checking netlist symbol footprint "Q74:/648A271C:Package_TO_SOT_SMD:SOT-23".
Info: Checking netlist symbol footprint "Q75:/64442829:Package_TO_SOT_SMD:SOT-23".
Info: Checking netlist symbol footprint "Q76:/610177AE:Package_TO_SOT_SMD:SOT-23".
Info: Checking netlist symbol footprint "Q77:/6F6B5917:Package_TO_SOT_SMD:SOT-23".
Info: Checking netlist symbol footprint "Q78:/6BB09031:Package_TO_SOT_SMD:SOT-23".
Info: Checking netlist symbol footprint "R351:/66BFD4B4:Resistor_SMD:R_0805_2012Metric".
Info: Checking netlist symbol footprint "Q79:/6BB081B4:Package_TO_SOT_SMD:SOT-23".
Info: Checking netlist symbol footprint "R350:/5683240B/6DB65FC7:Resistor_SMD:R_0805_2012Metric".
Info: Checking netlist symbol footprint "Q80:/6BB0381A:Package_TO_SOT_SMD:SOT-23".
Info: Checking netlist symbol footprint "R349:/5683240B/6DB65FC1:Resistor_SMD:R_0805_2012Metric".
Info: Checking netlist symbol footprint "R1:/696DF6FA:Resistor_SMD:R_0805_2012Metric".
Info: Checking netlist symbol footprint "R2:/696E0D13:Resistor_SMD:R_0805_2012Metric".
Info: Checking netlist symbol footprint "R3:/696E100E:Resistor_SMD:R_0805_2012Metric".
Info: Checking netlist symbol footprint "R4:/79C53C82:Resistor_SMD:R_0805_2012Metric".
Info: Checking netlist symbol footprint "R5:/696E1537:Resistor_SMD:R_0805_2012Metric".
Info: Checking netlist symbol footprint "R6:/656BCA0D:Resistor_SMD:R_0805_2012Metric".
Info: Checking netlist symbol footprint "R7:/5683240B/6BEC177C:Resistor_SMD:R_0805_2012Metric".
Info: Checking netlist symbol footprint "R8:/5683240B/6DD544C8:Resistor_SMD:R_0805_2012Metric".
Info: Checking netlist symbol footprint "R9:/5683240B/6F0967BB:Resistor_SMD:R_0805_2012Metric".
Info: Checking netlist symbol footprint "R10:/5683240B/700131EF:Resistor_SMD:R_0805_2012Metric".
Info: Checking netlist symbol footprint "R11:/5683240B/70BBDC96:Resistor_SMD:R_0805_2012Metric".
Info: Checking netlist symbol footprint "R12:/79C53C7C:Resistor_SMD:R_0805_2012Metric".
Info: Checking netlist symbol footprint "R13:/6BDF0EFF:Resistor_SMD:R_0805_2012Metric".
Info: Checking netlist symbol footprint "R14:/79C53C76:Resistor_SMD:R_0805_2012Metric".
Info: Checking netlist symbol footprint "R15:/A5517497:Resistor_SMD:R_0805_2012Metric".
Info: Checking netlist symbol footprint "R16:/6923E339:Resistor_SMD:R_0805_2012Metric".
Info: Checking netlist symbol footprint "R17:/64507A27:Resistor_SMD:R_0805_2012Metric".
Info: Checking netlist symbol footprint "R18:/6903A61A:Resistor_SMD:R_0805_2012Metric".
Info: Checking netlist symbol footprint "R19:/79C53C2A:Resistor_SMD:R_0805_2012Metric".
Info: Checking netlist symbol footprint "R20:/56B0AFF8:Resistor_SMD:R_0805_2012Metric".
Info: Checking netlist symbol footprint "R21:/56B09DC0:Resistor_SMD:R_0805_2012Metric".
Info: Checking netlist symbol footprint "R22:/68E2B2EA:Resistor_SMD:R_0805_2012Metric".
Info: Checking netlist symbol footprint "R23:/6AA599A9:Resistor_SMD:R_0805_2012Metric".
Info: Checking netlist symbol footprint "R24:/66B6DBAE:Resistor_SMD:R_0805_2012Metric".
Info: Checking netlist symbol footprint "R25:/66E6070D:Resistor_SMD:R_0805_2012Metric".
Info: Checking netlist symbol footprint "R26:/569CB992:Resistor_SMD:R_0805_2012Metric".
Info: Checking netlist symbol footprint "R27:/6AC84557:Resistor_SMD:R_0805_2012Metric".
Info: Checking netlist symbol footprint "R28:/66EA9D6D:Resistor_SMD:R_0805_2012Metric".
Info: Checking netlist symbol footprint "R29:/63DB59BC:Resistor_SMD:R_0805_2012Metric".
Info: Checking netlist symbol footprint "R30:/63DE5271:Resistor_SMD:R_0805_2012Metric".
Info: Checking netlist symbol footprint "R31:/66EAA52F:Resistor_SMD:R_0805_2012Metric".
Info: Checking netlist symbol footprint "R32:/6A57726D:Resistor_SMD:R_0805_2012Metric".
Info: Checking netlist symbol footprint "R33:/69E51601:Resistor_SMD:R_0805_2012Metric".
Info: Checking netlist symbol footprint "R34:/6A0D8743:Resistor_SMD:R_0805_2012Metric".
Info: Checking netlist symbol footprint "R35:/661F0659:Resistor_SMD:R_0805_2012Metric".
Info: Checking netlist symbol footprint "R36:/661F0058:Resistor_SMD:R_0805_2012Metric".
Info: Checking netlist symbol footprint "R37:/661EFEDE:Resistor_SMD:R_0805_2012Metric".
Info: Checking netlist symbol footprint "R38:/6617706F:Resistor_SMD:R_0805_2012Metric".
Info: Checking netlist symbol footprint "R39:/665771AB:Resistor_SMD:R_0805_2012Metric".
Info: Checking netlist symbol footprint "R40:/568CE415:Resistor_SMD:R_0805_2012Metric".
Info: Checking netlist symbol footprint "R41:/6ACFC3D6:Resistor_SMD:R_0805_2012Metric".
Info: Checking netlist symbol footprint "R42:/68E3AE19:Resistor_SMD:R_0805_2012Metric".
Info: Checking netlist symbol footprint "R43:/569B411B:Resistor_SMD:R_0805_2012Metric".
Info: Checking netlist symbol footprint "R44:/569B4EE3:Resistor_SMD:R_0805_2012Metric".
Info: Checking netlist symbol footprint "R45:/6ACFC403:Resistor_SMD:R_0805_2012Metric".
Info: Checking netlist symbol footprint "R46:/6ACFC409:Resistor_SMD:R_0805_2012Metric".
Info: Checking netlist symbol footprint "R47:/68BF3198:Resistor_SMD:R_0805_2012Metric".
Info: Checking netlist symbol footprint "R48:/79C53C24:Resistor_SMD:R_0805_2012Metric".
Info: Checking netlist symbol footprint "R49:/5690F474:Resistor_SMD:R_0805_2012Metric".
Info: Checking netlist symbol footprint "R50:/63AA1255:Resistor_SMD:R_0805_2012Metric".
Info: Checking netlist symbol footprint "R51:/63B53A22:Resistor_SMD:R_0805_2012Metric".
Info: Checking netlist symbol footprint "R52:/63B54BAC:Resistor_SMD:R_0805_2012Metric".
Info: Checking netlist symbol footprint "R53:/644B0DA7:Resistor_SMD:R_0805_2012Metric".
Info: Checking netlist symbol footprint "R54:/60E9A6AA:Resistor_SMD:R_0805_2012Metric".
Info: Checking netlist symbol footprint "R55:/65ADB6A4:Resistor_SMD:R_0805_2012Metric".
Info: Checking netlist symbol footprint "R56:/65ADAEE6:Resistor_SMD:R_0805_2012Metric".
Info: Checking netlist symbol footprint "R57:/65E62DC7:Resistor_SMD:R_0805_2012Metric".
Info: Checking netlist symbol footprint "R58:/79C53C1E:Resistor_SMD:R_0805_2012Metric".
Info: Checking netlist symbol footprint "R59:/605D9269:Resistor_SMD:R_0805_2012Metric".
Info: Checking netlist symbol footprint "R348:/5683240B/A34898DD:Resistor_SMD:R_0805_2012Metric".
Info: Checking netlist symbol footprint "R60:/60E82F7F:Resistor_SMD:R_0805_2012Metric".
Info: Checking netlist symbol footprint "R61:/60E2D218:Resistor_SMD:R_0805_2012Metric".
Info: Checking netlist symbol footprint "R62:/5683240B/64E39588:Resistor_SMD:R_2010_5025Metric".
Info: Checking netlist symbol footprint "R63:/6083C55B:Resistor_SMD:R_0805_2012Metric".
Info: Checking netlist symbol footprint "R64:/5683240B/64E395A7:Resistor_SMD:R_2010_5025Metric".
Info: Checking netlist symbol footprint "R65:/61E8BC6B:Resistor_SMD:R_0805_2012Metric".
Info: Checking netlist symbol footprint "R66:/65ADA7CA:Resistor_SMD:R_0805_2012Metric".
Info: Checking netlist symbol footprint "R67:/65AD9C98:Resistor_SMD:R_0805_2012Metric".
Info: Checking netlist symbol footprint "R68:/6074FC24:Resistor_SMD:R_0805_2012Metric".
Info: Checking netlist symbol footprint "R69:/6145179C:Resistor_SMD:R_0805_2012Metric".
Info: Checking netlist symbol footprint "R70:/6150E071:Resistor_SMD:R_0805_2012Metric".
Info: Checking netlist symbol footprint "R71:/614525D7:Resistor_SMD:R_0805_2012Metric".
Info: Checking netlist symbol footprint "R72:/61452300:Resistor_SMD:R_0805_2012Metric".
Info: Checking netlist symbol footprint "R73:/7008E38B:Resistor_SMD:R_0805_2012Metric".
Info: Checking netlist symbol footprint "R347:/5683240B/6D777CC4:Resistor_SMD:R_0805_2012Metric".
Info: Checking netlist symbol footprint "R346:/5683240B/6D777CBE:Resistor_SMD:R_0805_2012Metric".
Info: Changing component path "R73:/6074F414" to "/7008E38B".
Info: Checking netlist symbol footprint "R74:/60D2D504:Resistor_SMD:R_0805_2012Metric".
Info: Checking netlist symbol footprint "R75:/611E19A1:Resistor_SMD:R_0805_2012Metric".
Info: Checking netlist symbol footprint "R76:/6CB824B9:Resistor_SMD:R_0805_2012Metric".
Info: Checking netlist symbol footprint "R345:/5683240B/A306A52F:Resistor_SMD:R_0805_2012Metric".
Info: Checking netlist symbol footprint "R344:/5683240B/6CBACC57:Resistor_SMD:R_0805_2012Metric".
Info: Changing component path "R76:/605DCEC5" to "/6CB824B9".
Info: Checking netlist symbol footprint "R343:/5683240B/6CBACC51:Resistor_SMD:R_0805_2012Metric".
Info: Checking netlist symbol footprint "R342:/5683240B/6C7BCC52:Resistor_SMD:R_0805_2012Metric".
Info: Checking netlist symbol footprint "R77:/611E1FCB:Resistor_SMD:R_0805_2012Metric".
Info: Checking netlist symbol footprint "R78:/611E2977:Resistor_SMD:R_0805_2012Metric".
Info: Checking netlist symbol footprint "R79:/60DD6B9B:Resistor_SMD:R_0805_2012Metric".
Info: Checking netlist symbol footprint "R80:/7960BF3A:Resistor_SMD:R_0805_2012Metric".
Info: Checking netlist symbol footprint "R81:/866258AA:Resistor_SMD:R_0805_2012Metric".
Info: Checking netlist symbol footprint "R82:/94851341:Resistor_SMD:R_0805_2012Metric".
Info: Checking netlist symbol footprint "R83:/5683240B/56843AFF:Resistor_SMD:R_2010_5025Metric".
Info: Checking netlist symbol footprint "R84:/5683240B/56845053:Resistor_SMD:R_2010_5025Metric".
Info: Checking netlist symbol footprint "R85:/5683240B/56845521:Resistor_SMD:R_2010_5025Metric".
Info: Checking netlist symbol footprint "R86:/5683240B/5684554C:Resistor_SMD:R_2010_5025Metric".
Info: Checking netlist symbol footprint "R87:/5683240B/56846357:Resistor_SMD:R_2010_5025Metric".
Info: Checking netlist symbol footprint "R88:/5683240B/56846382:Resistor_SMD:R_2010_5025Metric".
Info: Checking netlist symbol footprint "R89:/5683240B/568463AD:Resistor_SMD:R_2010_5025Metric".
Info: Checking netlist symbol footprint "R90:/5683240B/568463D8:Resistor_SMD:R_2010_5025Metric".
Info: Checking netlist symbol footprint "R91:/5683240B/56846FED:Resistor_SMD:R_2010_5025Metric".
Info: Checking netlist symbol footprint "R92:/5683240B/56847018:Resistor_SMD:R_2010_5025Metric".
Info: Checking netlist symbol footprint "R93:/5683240B/56847043:Resistor_SMD:R_2010_5025Metric".
Info: Checking netlist symbol footprint "R94:/5683240B/5684706E:Resistor_SMD:R_2010_5025Metric".
Info: Checking netlist symbol footprint "R95:/5683240B/56843AB8:Resistor_SMD:R_0805_2012Metric".
Info: Checking netlist symbol footprint "R96:/5683240B/5684504D:Resistor_SMD:R_0805_2012Metric".
Info: Checking netlist symbol footprint "R97:/5683240B/5684551B:Resistor_SMD:R_0805_2012Metric".
Info: Checking netlist symbol footprint "R98:/5683240B/56845546:Resistor_SMD:R_0805_2012Metric".
Info: Checking netlist symbol footprint "R99:/5683240B/56846351:Resistor_SMD:R_0805_2012Metric".
Info: Checking netlist symbol footprint "R100:/5683240B/5684637C:Resistor_SMD:R_0805_2012Metric".
Info: Checking netlist symbol footprint "R101:/5683240B/568463A7:Resistor_SMD:R_0805_2012Metric".
Info: Checking netlist symbol footprint "R102:/5683240B/568463D2:Resistor_SMD:R_0805_2012Metric".
Info: Checking netlist symbol footprint "R103:/5683240B/56846FE7:Resistor_SMD:R_0805_2012Metric".
Info: Checking netlist symbol footprint "R104:/5683240B/56847012:Resistor_SMD:R_0805_2012Metric".
Info: Checking netlist symbol footprint "R105:/5683240B/5684703D:Resistor_SMD:R_0805_2012Metric".
Info: Checking netlist symbol footprint "R106:/5683240B/56847068:Resistor_SMD:R_0805_2012Metric".
Info: Checking netlist symbol footprint "R107:/5683240B/568560CC:Resistor_SMD:R_0805_2012Metric".
Info: Checking netlist symbol footprint "R108:/5683240B/56843B7B:Resistor_SMD:R_0805_2012Metric".
Info: Checking netlist symbol footprint "R109:/5683240B/56845059:Resistor_SMD:R_0805_2012Metric".
Info: Checking netlist symbol footprint "R110:/5683240B/56845527:Resistor_SMD:R_0805_2012Metric".
Info: Checking netlist symbol footprint "R111:/5683240B/56845552:Resistor_SMD:R_0805_2012Metric".
Info: Checking netlist symbol footprint "R112:/5683240B/5684635D:Resistor_SMD:R_0805_2012Metric".
Info: Checking netlist symbol footprint "R113:/5683240B/56846388:Resistor_SMD:R_0805_2012Metric".
Info: Checking netlist symbol footprint "R114:/5683240B/568463B3:Resistor_SMD:R_0805_2012Metric".
Info: Checking netlist symbol footprint "R115:/5683240B/568463DE:Resistor_SMD:R_0805_2012Metric".
Info: Checking netlist symbol footprint "R116:/5683240B/56846FF3:Resistor_SMD:R_0805_2012Metric".
Info: Checking netlist symbol footprint "R117:/5683240B/5684701E:Resistor_SMD:R_0805_2012Metric".
Info: Checking netlist symbol footprint "R118:/5683240B/56847049:Resistor_SMD:R_0805_2012Metric".
Info: Checking netlist symbol footprint "R119:/5683240B/56847074:Resistor_SMD:R_0805_2012Metric".
Info: Checking netlist symbol footprint "R120:/5683240B/569E2365:Resistor_SMD:R_0805_2012Metric".
Info: Checking netlist symbol footprint "R121:/95943D18:Resistor_SMD:R_0805_2012Metric".
Info: Checking netlist symbol footprint "R122:/5683240B/569E236B:Resistor_SMD:R_0805_2012Metric".
Info: Checking netlist symbol footprint "R123:/5683240B/5685A2BE:Resistor_SMD:R_0805_2012Metric".
Info: Checking netlist symbol footprint "R124:/5683240B/56857DD6:Resistor_SMD:R_0805_2012Metric".
Info: Checking netlist symbol footprint "R125:/5683240B/7F5B2042:Resistor_SMD:R_0805_2012Metric".
Info: Checking netlist symbol footprint "R126:/5683240B/568792C4:Resistor_SMD:R_0805_2012Metric".
Info: Checking netlist symbol footprint "R127:/5683240B/56A8A34D:Resistor_SMD:R_0805_2012Metric".
Info: Checking netlist symbol footprint "R128:/5683240B/568793DC:Resistor_SMD:R_0805_2012Metric".
Info: Checking netlist symbol footprint "R129:/5683240B/780E28EB:Resistor_SMD:R_1206_3216Metric".
Info: Checking netlist symbol footprint "R130:/5683240B/7139024E:Resistor_SMD:R_1206_3216Metric".
Info: Checking netlist symbol footprint "R341:/5683240B/6C3D2D11:Resistor_SMD:R_0805_2012Metric".
Info: Checking netlist symbol footprint "R131:/5683240B/780E1FCB:Resistor_SMD:R_1206_3216Metric".
Info: Checking netlist symbol footprint "R132:/5683240B/56889896:Resistor_SMD:R_2010_5025Metric".
Info: Checking netlist symbol footprint "R133:/5683240B/568898B5:Resistor_SMD:R_2010_5025Metric".
Info: Checking netlist symbol footprint "R134:/5683240B/568898D4:Resistor_SMD:R_2010_5025Metric".
Info: Checking netlist symbol footprint "R135:/5683240B/568898F3:Resistor_SMD:R_2010_5025Metric".
Info: Checking netlist symbol footprint "R136:/5683240B/56889912:Resistor_SMD:R_2010_5025Metric".
Info: Checking netlist symbol footprint "R137:/5683240B/56889931:Resistor_SMD:R_2010_5025Metric".
Info: Checking netlist symbol footprint "R138:/5683240B/56889950:Resistor_SMD:R_2010_5025Metric".
Info: Checking netlist symbol footprint "R139:/5683240B/5688996F:Resistor_SMD:R_2010_5025Metric".
Info: Checking netlist symbol footprint "R140:/5683240B/5688998E:Resistor_SMD:R_2010_5025Metric".
Info: Checking netlist symbol footprint "R141:/5683240B/568899AD:Resistor_SMD:R_2010_5025Metric".
Info: Checking netlist symbol footprint "R142:/5683240B/568899CC:Resistor_SMD:R_2010_5025Metric".
Info: Checking netlist symbol footprint "R143:/5683240B/568899EB:Resistor_SMD:R_2010_5025Metric".
Info: Checking netlist symbol footprint "R144:/5683240B/56889890:Resistor_SMD:R_0805_2012Metric".
Info: Checking netlist symbol footprint "R145:/5683240B/568898AF:Resistor_SMD:R_0805_2012Metric".
Info: Checking netlist symbol footprint "R146:/5683240B/568898CE:Resistor_SMD:R_0805_2012Metric".
Info: Checking netlist symbol footprint "R147:/5683240B/568898ED:Resistor_SMD:R_0805_2012Metric".
Info: Checking netlist symbol footprint "R148:/5683240B/5688990C:Resistor_SMD:R_0805_2012Metric".
Info: Checking netlist symbol footprint "R149:/5683240B/5688992B:Resistor_SMD:R_0805_2012Metric".
Info: Checking netlist symbol footprint "R150:/5683240B/5688994A:Resistor_SMD:R_0805_2012Metric".
Info: Checking netlist symbol footprint "R151:/5683240B/56889969:Resistor_SMD:R_0805_2012Metric".
Info: Checking netlist symbol footprint "R152:/5683240B/56889988:Resistor_SMD:R_0805_2012Metric".
Info: Checking netlist symbol footprint "R153:/5683240B/568899A7:Resistor_SMD:R_0805_2012Metric".
Info: Checking netlist symbol footprint "R154:/5683240B/568899C6:Resistor_SMD:R_0805_2012Metric".
Info: Checking netlist symbol footprint "R155:/5683240B/568899E5:Resistor_SMD:R_0805_2012Metric".
Info: Checking netlist symbol footprint "R156:/5683240B/56889A04:Resistor_SMD:R_0805_2012Metric".
Info: Checking netlist symbol footprint "R157:/5683240B/5688989C:Resistor_SMD:R_0805_2012Metric".
Info: Checking netlist symbol footprint "R158:/5683240B/568898BB:Resistor_SMD:R_0805_2012Metric".
Info: Checking netlist symbol footprint "R159:/5683240B/568898DA:Resistor_SMD:R_0805_2012Metric".
Info: Checking netlist symbol footprint "R160:/5683240B/568898F9:Resistor_SMD:R_0805_2012Metric".
Info: Checking netlist symbol footprint "R161:/5683240B/56889918:Resistor_SMD:R_0805_2012Metric".
Info: Checking netlist symbol footprint "R162:/5683240B/56889937:Resistor_SMD:R_0805_2012Metric".
Info: Checking netlist symbol footprint "R163:/5683240B/56889956:Resistor_SMD:R_0805_2012Metric".
Info: Checking netlist symbol footprint "R164:/5683240B/56889975:Resistor_SMD:R_0805_2012Metric".
Info: Checking netlist symbol footprint "R165:/5683240B/56889994:Resistor_SMD:R_0805_2012Metric".
Info: Checking netlist symbol footprint "R166:/5683240B/568899B3:Resistor_SMD:R_0805_2012Metric".
Info: Checking netlist symbol footprint "R167:/5683240B/568899D2:Resistor_SMD:R_0805_2012Metric".
Info: Checking netlist symbol footprint "R168:/5683240B/568899F1:Resistor_SMD:R_0805_2012Metric".
Info: Checking netlist symbol footprint "R169:/5683240B/56889A1C:Resistor_SMD:R_0805_2012Metric".
Info: Checking netlist symbol footprint "R170:/5683240B/56889A10:Resistor_SMD:R_0805_2012Metric".
Info: Checking netlist symbol footprint "R171:/5683240B/8B1C6F4D:Resistor_SMD:R_0805_2012Metric".
Info: Checking netlist symbol footprint "R172:/5683240B/56889B8D:Resistor_SMD:R_0805_2012Metric".
Info: Checking netlist symbol footprint "R173:/5683240B/56A908DF:Resistor_SMD:R_0805_2012Metric".
Info: Checking netlist symbol footprint "R174:/5683240B/56889B93:Resistor_SMD:R_0805_2012Metric".
Info: Checking netlist symbol footprint "R175:/5683240B/7ECE4688:Resistor_SMD:R_1206_3216Metric".
Info: Checking netlist symbol footprint "R176:/5683240B/7ECE468E:Resistor_SMD:R_1206_3216Metric".
Info: Checking netlist symbol footprint "R177:/5683240B/56892AC5:Resistor_SMD:R_2010_5025Metric".
Info: Checking netlist symbol footprint "R178:/5683240B/56892AE4:Resistor_SMD:R_2010_5025Metric".
Info: Checking netlist symbol footprint "R179:/5683240B/56892B03:Resistor_SMD:R_2010_5025Metric".
Info: Checking netlist symbol footprint "R180:/5683240B/56892B22:Resistor_SMD:R_2010_5025Metric".
Info: Checking netlist symbol footprint "R181:/5683240B/56892B41:Resistor_SMD:R_2010_5025Metric".
Info: Checking netlist symbol footprint "R182:/5683240B/56892B60:Resistor_SMD:R_2010_5025Metric".
Info: Checking netlist symbol footprint "R183:/5683240B/56892B7F:Resistor_SMD:R_2010_5025Metric".
Info: Checking netlist symbol footprint "R184:/5683240B/56892B9E:Resistor_SMD:R_2010_5025Metric".
Info: Checking netlist symbol footprint "R185:/5683240B/56892BBD:Resistor_SMD:R_2010_5025Metric".
Info: Checking netlist symbol footprint "R186:/5683240B/56892BDC:Resistor_SMD:R_2010_5025Metric".
Info: Checking netlist symbol footprint "R187:/5683240B/56892BFB:Resistor_SMD:R_2010_5025Metric".
Info: Checking netlist symbol footprint "R188:/5683240B/56892C1A:Resistor_SMD:R_2010_5025Metric".
Info: Checking netlist symbol footprint "R189:/5683240B/56892ABF:Resistor_SMD:R_0805_2012Metric".
Info: Checking netlist symbol footprint "R190:/5683240B/56892ADE:Resistor_SMD:R_0805_2012Metric".
Info: Checking netlist symbol footprint "R191:/5683240B/56892AFD:Resistor_SMD:R_0805_2012Metric".
Info: Checking netlist symbol footprint "R192:/5683240B/56892B1C:Resistor_SMD:R_0805_2012Metric".
Info: Checking netlist symbol footprint "R193:/5683240B/56892B3B:Resistor_SMD:R_0805_2012Metric".
Info: Checking netlist symbol footprint "R194:/5683240B/56892B5A:Resistor_SMD:R_0805_2012Metric".
Info: Checking netlist symbol footprint "R195:/5683240B/56892B79:Resistor_SMD:R_0805_2012Metric".
Info: Checking netlist symbol footprint "R196:/5683240B/56892B98:Resistor_SMD:R_0805_2012Metric".
Info: Checking netlist symbol footprint "R197:/5683240B/56892BB7:Resistor_SMD:R_0805_2012Metric".
Info: Checking netlist symbol footprint "R198:/5683240B/56892BD6:Resistor_SMD:R_0805_2012Metric".
Info: Checking netlist symbol footprint "R199:/5683240B/56892BF5:Resistor_SMD:R_0805_2012Metric".
Info: Checking netlist symbol footprint "R200:/5683240B/56892C14:Resistor_SMD:R_0805_2012Metric".
Info: Checking netlist symbol footprint "R201:/5683240B/56892C33:Resistor_SMD:R_0805_2012Metric".
Info: Checking netlist symbol footprint "R202:/5683240B/56892ACB:Resistor_SMD:R_0805_2012Metric".
Info: Checking netlist symbol footprint "R203:/5683240B/56892AEA:Resistor_SMD:R_0805_2012Metric".
Info: Checking netlist symbol footprint "R204:/5683240B/56892B09:Resistor_SMD:R_0805_2012Metric".
Info: Checking netlist symbol footprint "R205:/5683240B/56892B28:Resistor_SMD:R_0805_2012Metric".
Info: Checking netlist symbol footprint "R206:/5683240B/56892B47:Resistor_SMD:R_0805_2012Metric".
Info: Checking netlist symbol footprint "R207:/5683240B/56892B66:Resistor_SMD:R_0805_2012Metric".
Info: Checking netlist symbol footprint "R208:/5683240B/56892B85:Resistor_SMD:R_0805_2012Metric".
Info: Checking netlist symbol footprint "R209:/5683240B/56892BA4:Resistor_SMD:R_0805_2012Metric".
Info: Checking netlist symbol footprint "R210:/5683240B/56892BC3:Resistor_SMD:R_0805_2012Metric".
Info: Checking netlist symbol footprint "R211:/5683240B/56892BE2:Resistor_SMD:R_0805_2012Metric".
Info: Checking netlist symbol footprint "R212:/5683240B/56892C01:Resistor_SMD:R_0805_2012Metric".
Info: Checking netlist symbol footprint "R213:/5683240B/56892C20:Resistor_SMD:R_0805_2012Metric".
Info: Checking netlist symbol footprint "R214:/5683240B/7F1C7FF9:Resistor_SMD:R_1206_3216Metric".
Info: Checking netlist symbol footprint "R215:/5683240B/7F1C7FFF:Resistor_SMD:R_1206_3216Metric".
Info: Checking netlist symbol footprint "R216:/5683240B/56892C4B:Resistor_SMD:R_0805_2012Metric".
Info: Checking netlist symbol footprint "R217:/5683240B/56892C3F:Resistor_SMD:R_0805_2012Metric".
Info: Checking netlist symbol footprint "R218:/5683240B/8BB7BEED:Resistor_SMD:R_0805_2012Metric".
Info: Checking netlist symbol footprint "R219:/5683240B/56892DBC:Resistor_SMD:R_0805_2012Metric".
Info: Checking netlist symbol footprint "R220:/5683240B/56A92DA3:Resistor_SMD:R_0805_2012Metric".
Info: Checking netlist symbol footprint "R221:/5683240B/56892DC2:Resistor_SMD:R_0805_2012Metric".
Info: Checking netlist symbol footprint "R222:/5683240B/7F444B0D:Resistor_SMD:R_1206_3216Metric".
Info: Checking netlist symbol footprint "R223:/5683240B/847E2838:Resistor_SMD:R_0805_2012Metric".
Info: Checking netlist symbol footprint "R224:/5683240B/7F444B13:Resistor_SMD:R_1206_3216Metric".
Info: Checking netlist symbol footprint "R225:/5683240B/724A6289:Resistor_SMD:R_2010_5025Metric".
Info: Checking netlist symbol footprint "R226:/5683240B/724A62A8:Resistor_SMD:R_2010_5025Metric".
Info: Checking netlist symbol footprint "R227:/5683240B/724A62C7:Resistor_SMD:R_2010_5025Metric".
Info: Checking netlist symbol footprint "R228:/5683240B/724A62E6:Resistor_SMD:R_2010_5025Metric".
Info: Checking netlist symbol footprint "R229:/5683240B/724A6305:Resistor_SMD:R_2010_5025Metric".
Info: Checking netlist symbol footprint "R230:/5683240B/724A6324:Resistor_SMD:R_2010_5025Metric".
Info: Checking netlist symbol footprint "R231:/5683240B/724A6343:Resistor_SMD:R_2010_5025Metric".
Info: Checking netlist symbol footprint "R232:/5683240B/724A6362:Resistor_SMD:R_2010_5025Metric".
Info: Checking netlist symbol footprint "R233:/5683240B/724A6381:Resistor_SMD:R_2010_5025Metric".
Info: Checking netlist symbol footprint "R234:/5683240B/724A63A0:Resistor_SMD:R_2010_5025Metric".
Info: Checking netlist symbol footprint "R235:/5683240B/724A63BF:Resistor_SMD:R_2010_5025Metric".
Info: Checking netlist symbol footprint "R236:/5683240B/724A63DE:Resistor_SMD:R_2010_5025Metric".
Info: Checking netlist symbol footprint "R237:/5683240B/724A6283:Resistor_SMD:R_0805_2012Metric".
Info: Checking netlist symbol footprint "R238:/5683240B/724A62A2:Resistor_SMD:R_0805_2012Metric".
Info: Checking netlist symbol footprint "R239:/5683240B/724A62C1:Resistor_SMD:R_0805_2012Metric".
Info: Checking netlist symbol footprint "R240:/5683240B/724A62E0:Resistor_SMD:R_0805_2012Metric".
Info: Checking netlist symbol footprint "R241:/5683240B/724A62FF:Resistor_SMD:R_0805_2012Metric".
Info: Checking netlist symbol footprint "R242:/5683240B/724A631E:Resistor_SMD:R_0805_2012Metric".
Info: Checking netlist symbol footprint "R243:/5683240B/724A633D:Resistor_SMD:R_0805_2012Metric".
Info: Checking netlist symbol footprint "R244:/5683240B/724A635C:Resistor_SMD:R_0805_2012Metric".
Info: Checking netlist symbol footprint "R245:/5683240B/724A637B:Resistor_SMD:R_0805_2012Metric".
Info: Checking netlist symbol footprint "R246:/5683240B/724A639A:Resistor_SMD:R_0805_2012Metric".
Info: Checking netlist symbol footprint "R247:/5683240B/724A63B9:Resistor_SMD:R_0805_2012Metric".
Info: Checking netlist symbol footprint "R248:/5683240B/724A63D8:Resistor_SMD:R_0805_2012Metric".
Info: Checking netlist symbol footprint "R249:/5683240B/724A63F7:Resistor_SMD:R_0805_2012Metric".
Info: Checking netlist symbol footprint "R250:/5683240B/724A628F:Resistor_SMD:R_0805_2012Metric".
Info: Checking netlist symbol footprint "R251:/5683240B/724A62AE:Resistor_SMD:R_0805_2012Metric".
Info: Checking netlist symbol footprint "R252:/5683240B/724A62CD:Resistor_SMD:R_0805_2012Metric".
Info: Checking netlist symbol footprint "R253:/5683240B/724A62EC:Resistor_SMD:R_0805_2012Metric".
Info: Checking netlist symbol footprint "R254:/5683240B/724A630B:Resistor_SMD:R_0805_2012Metric".
Info: Checking netlist symbol footprint "R255:/5683240B/724A632A:Resistor_SMD:R_0805_2012Metric".
Info: Checking netlist symbol footprint "R256:/5683240B/724A6349:Resistor_SMD:R_0805_2012Metric".
Info: Checking netlist symbol footprint "R257:/5683240B/724A6368:Resistor_SMD:R_0805_2012Metric".
Info: Checking netlist symbol footprint "R258:/5683240B/724A6387:Resistor_SMD:R_0805_2012Metric".
Info: Checking netlist symbol footprint "R259:/5683240B/724A63A6:Resistor_SMD:R_0805_2012Metric".
Info: Checking netlist symbol footprint "R260:/5683240B/724A63C5:Resistor_SMD:R_0805_2012Metric".
Info: Checking netlist symbol footprint "R261:/5683240B/724A63E4:Resistor_SMD:R_0805_2012Metric".
Info: Checking netlist symbol footprint "R262:/5683240B/724A6409:Resistor_SMD:R_0805_2012Metric".
Info: Checking netlist symbol footprint "R263:/5683240B/724A6403:Resistor_SMD:R_0805_2012Metric".
Info: Checking netlist symbol footprint "R264:/5683240B/8BDE7AF4:Resistor_SMD:R_0805_2012Metric".
Info: Checking netlist symbol footprint "R265:/5683240B/724A6430:Resistor_SMD:R_0805_2012Metric".
Info: Checking netlist symbol footprint "R266:/5683240B/724A65D3:Resistor_SMD:R_0805_2012Metric".
Info: Checking netlist symbol footprint "R267:/5683240B/724A6436:Resistor_SMD:R_0805_2012Metric".
Info: Checking netlist symbol footprint "R268:/5683240B/64E395C6:Resistor_SMD:R_2010_5025Metric".
Info: Checking netlist symbol footprint "R269:/5683240B/64E395E5:Resistor_SMD:R_2010_5025Metric".
Info: Checking netlist symbol footprint "R270:/5683240B/64E39604:Resistor_SMD:R_2010_5025Metric".
Info: Checking netlist symbol footprint "R271:/5683240B/64E39623:Resistor_SMD:R_2010_5025Metric".
Info: Checking netlist symbol footprint "R272:/5683240B/64E39642:Resistor_SMD:R_2010_5025Metric".
Info: Checking netlist symbol footprint "R273:/5683240B/64E39661:Resistor_SMD:R_2010_5025Metric".
Info: Checking netlist symbol footprint "R274:/5683240B/64E39680:Resistor_SMD:R_2010_5025Metric".
Info: Checking netlist symbol footprint "R275:/5683240B/64E3969F:Resistor_SMD:R_2010_5025Metric".
Info: Checking netlist symbol footprint "R276:/5683240B/64E396BE:Resistor_SMD:R_2010_5025Metric".
Info: Checking netlist symbol footprint "R277:/5683240B/64E396DD:Resistor_SMD:R_2010_5025Metric".
Info: Checking netlist symbol footprint "R278:/5683240B/64E39582:Resistor_SMD:R_0805_2012Metric".
Info: Checking netlist symbol footprint "R279:/5683240B/64E395A1:Resistor_SMD:R_0805_2012Metric".
Info: Checking netlist symbol footprint "R280:/5683240B/64E395C0:Resistor_SMD:R_0805_2012Metric".
Info: Checking netlist symbol footprint "R281:/5683240B/64E395DF:Resistor_SMD:R_0805_2012Metric".
Info: Checking netlist symbol footprint "R282:/5683240B/64E395FE:Resistor_SMD:R_0805_2012Metric".
Info: Checking netlist symbol footprint "R283:/5683240B/64E3961D:Resistor_SMD:R_0805_2012Metric".
Info: Checking netlist symbol footprint "R284:/5683240B/64E3963C:Resistor_SMD:R_0805_2012Metric".
Info: Checking netlist symbol footprint "R285:/5683240B/64E3965B:Resistor_SMD:R_0805_2012Metric".
Info: Checking netlist symbol footprint "R286:/5683240B/64E3967A:Resistor_SMD:R_0805_2012Metric".
Info: Checking netlist symbol footprint "R287:/5683240B/64E39699:Resistor_SMD:R_0805_2012Metric".
Info: Checking netlist symbol footprint "R288:/5683240B/64E396B8:Resistor_SMD:R_0805_2012Metric".
Info: Checking netlist symbol footprint "R289:/5683240B/64E396D7:Resistor_SMD:R_0805_2012Metric".
Info: Checking netlist symbol footprint "R290:/5683240B/64E396F6:Resistor_SMD:R_0805_2012Metric".
Info: Checking netlist symbol footprint "R291:/5683240B/64E3958E:Resistor_SMD:R_0805_2012Metric".
Info: Checking netlist symbol footprint "R292:/5683240B/64E395AD:Resistor_SMD:R_0805_2012Metric".
Info: Checking netlist symbol footprint "R293:/5683240B/64E395CC:Resistor_SMD:R_0805_2012Metric".
Info: Checking netlist symbol footprint "R294:/5683240B/64E395EB:Resistor_SMD:R_0805_2012Metric".
Info: Checking netlist symbol footprint "R295:/5683240B/64E3960A:Resistor_SMD:R_0805_2012Metric".
Info: Checking netlist symbol footprint "R296:/5683240B/64E39629:Resistor_SMD:R_0805_2012Metric".
Info: Checking netlist symbol footprint "R297:/5683240B/64E39648:Resistor_SMD:R_0805_2012Metric".
Info: Checking netlist symbol footprint "R298:/5683240B/64E39667:Resistor_SMD:R_0805_2012Metric".
Info: Checking netlist symbol footprint "R299:/5683240B/64E39686:Resistor_SMD:R_0805_2012Metric".
Info: Checking netlist symbol footprint "R300:/5683240B/64E396A5:Resistor_SMD:R_0805_2012Metric".
Info: Checking netlist symbol footprint "R301:/5683240B/64E396C4:Resistor_SMD:R_0805_2012Metric".
Info: Checking netlist symbol footprint "R302:/5683240B/64E396E3:Resistor_SMD:R_0805_2012Metric".
Info: Checking netlist symbol footprint "R303:/5683240B/64E39708:Resistor_SMD:R_0805_2012Metric".
Info: Checking netlist symbol footprint "R304:/5683240B/64E39702:Resistor_SMD:R_0805_2012Metric".
Info: Checking netlist symbol footprint "R305:/5683240B/64E39A0F:Resistor_SMD:R_0805_2012Metric".
Info: Checking netlist symbol footprint "R306:/5683240B/64E3972E:Resistor_SMD:R_0805_2012Metric".
Info: Checking netlist symbol footprint "R307:/5683240B/64E39896:Resistor_SMD:R_0805_2012Metric".
Info: Checking netlist symbol footprint "R308:/5683240B/64E39734:Resistor_SMD:R_0805_2012Metric".
Info: Checking netlist symbol footprint "R309:/5683240B/677DA392:Resistor_SMD:R_1206_3216Metric".
Info: Checking netlist symbol footprint "R310:/5683240B/677DB1E6:Resistor_SMD:R_1206_3216Metric".
Info: Checking netlist symbol footprint "R311:/60B1A00F:Resistor_SMD:R_0805_2012Metric".
Info: Checking netlist symbol footprint "R312:/6291134F:Resistor_SMD:R_0805_2012Metric".
Info: Checking netlist symbol footprint "R313:/95943D1E:Resistor_SMD:R_0805_2012Metric".
Info: Checking netlist symbol footprint "R314:/95DD44B8:Resistor_SMD:R_0805_2012Metric".
Info: Checking netlist symbol footprint "R315:/61809CBE:Resistor_SMD:R_0805_2012Metric".
Info: Checking netlist symbol footprint "R316:/61D94DDE:Resistor_SMD:R_0805_2012Metric".
Info: Checking netlist symbol footprint "R317:/9DDBD922:Resistor_SMD:R_0805_2012Metric".
Info: Checking netlist symbol footprint "R318:/9E440EC8:Resistor_SMD:R_0805_2012Metric".
Info: Checking netlist symbol footprint "R319:/64C39F2B:Resistor_SMD:R_0805_2012Metric".
Info: Checking netlist symbol footprint "R320:/660B894A:Resistor_SMD:R_0805_2012Metric".
Info: Checking netlist symbol footprint "R321:/9DDBD928:Resistor_SMD:R_0805_2012Metric".
Info: Checking netlist symbol footprint "R322:/9E440ECE:Resistor_SMD:R_0805_2012Metric".
Info: Checking netlist symbol footprint "R323:/66B908BE:Resistor_SMD:R_0805_2012Metric".
Info: Checking netlist symbol footprint "R324:/67A025A5:Resistor_SMD:R_0805_2012Metric".
Info: Checking netlist symbol footprint "R325:/9DAF2723:Resistor_SMD:R_0805_2012Metric".
Info: Checking netlist symbol footprint "R326:/9DAF156A:Resistor_SMD:R_0805_2012Metric".
Info: Checking netlist symbol footprint "R327:/7C2DC154:Resistor_SMD:R_0805_2012Metric".
Info: Checking netlist symbol footprint "R328:/672AE8A2:Resistor_SMD:R_0805_2012Metric".
Info: Checking netlist symbol footprint "R329:/675667AA:Resistor_SMD:R_0805_2012Metric".
Info: Checking netlist symbol footprint "R330:/643C5BBC:Resistor_SMD:R_0805_2012Metric".
Info: Checking netlist symbol footprint "R331:/66BFC795:Resistor_SMD:R_0805_2012Metric".
Info: Checking netlist symbol footprint "R340:/5683240B/73620220:Resistor_SMD:R_0805_2012Metric".
Info: Checking netlist symbol footprint "R332:/65368E59:Resistor_SMD:R_0805_2012Metric".
Info: Checking netlist symbol footprint "R333:/643C56C4:Resistor_SMD:R_0805_2012Metric".
Info: Checking netlist symbol footprint "R334:/887523D0:Resistor_SMD:R_0805_2012Metric".
Info: Checking netlist symbol footprint "R339:/5683240B/73620226:Resistor_SMD:R_0805_2012Metric".
Info: Checking netlist symbol footprint "R335:/6309442A:Resistor_SMD:R_0805_2012Metric".
Info: Checking netlist symbol footprint "R336:/631417AB:Resistor_SMD:R_0805_2012Metric".
Info: Checking netlist symbol footprint "R337:/64C9E830:Resistor_SMD:R_0805_2012Metric".
Info: Checking netlist symbol footprint "R338:/5683240B/A01F17EB:Resistor_SMD:R_0805_2012Metric".
Changing footprint R334 value from 100 to 20.
Adding new symbol R331 footprint Resistor_SMD:R_0805_2012Metric.
Changing symbol R130 footprint from Resistor_SMD:R_0805_2012Metric to Resistor_SMD:R_1206_3216Metric.
Changing footprint R76 pad 1 net from /SNUB to +12V.
Changing footprint R76 pad 2 net from /L1 to GND_ENG.
Changing footprint R76 value from DNP to DNP(0).
Changing symbol R76 footprint from Resistor_SMD:R_2010_5025Metric to Resistor_SMD:R_0805_2012Metric.
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

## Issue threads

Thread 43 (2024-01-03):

Initial Brainstorming for Lifetime Ah Counters

doppelhub, 2024-01-03:
I want to add two "lifetime mAh" accumulators: one for assist and another for regen. To minimize EEPROM write cycles, each accumulator is a uint16 in RAM.

To prevent losing this data, we need to write each value in RAM to EEPROM whenever any of the following occur:
-keyOff event occurs, or;
-grid charger unplug event occurs, or;
-an accumulator is close to full (e.g. greater than 65000), or;
-24 hours have elapsed since the last EEPROM update.

Each time we write RAM value to EEPROM, we immediately set the RAM value back to 0.

Each EEPROM accumulator (assist and regen) is uint32, with each count being 1 mAh. Therefore, each EEPROM accumulator can count up to 4.3 MAh, which is way more than we'll ever need.

Use EEPROM.update - instead of EEPROM.write - to reduce write wear on the EEPROM.

Finally, we need a way for the customer to reset both lifetime values in EEPROM... "$TESTE" is an existing method to do this... probably makes sense to just add the clearing code to that existing function... and probably make it a little harder for the customer to accidentally reset all these values (if they accidentally type "$TESTE"). The easiest safeguard to implement is probably just requiring the user to enter "$TESTE" twice in a five second period (i.e. the first thing $TESTE does is look to see when the latest TESTE was received, and if it was more than five seconds it would say "Type '$TESTE' again within five seconds to reset all EEPROM data"... that's non-blocking and non-modal.

...

To display this lifetime mAh data to the customer, I propose we add it to the "$TESTW" command, which displays battery temp and SoC history. Something like:
Lifetime Assist: 123.456 Ah
Lifetime Regen: 234.567 Ah

Note that $TESTW would need to read each value (assist and regen) from EEPROM, and then also add the corresponding value in RAM. Otherwise, we'd miss the residual mAh stored in RAM.

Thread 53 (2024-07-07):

Bug (?): LiBCM reboots on USB plug-in after first boot

Hurricos, 2024-07-07:
Configuration: 48S FoMoCo, firmware 2024MAY01 (commit fccb093ef208934fdf88053db07fbeda600f861f).

If I turn the IMA switch on, start the car, then plug in the USB cable, LiBCM reboots, resetting SoC to 6%.

Hurricos, 2024-07-07:
Mea culpa. This "bug" is the standard behavior of the Arduino IDE, not a bug in LiBCM.

Closed 2024-07-07.

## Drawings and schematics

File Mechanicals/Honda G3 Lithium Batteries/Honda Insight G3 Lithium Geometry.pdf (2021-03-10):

These dimensions measured by hand with a tape measure.

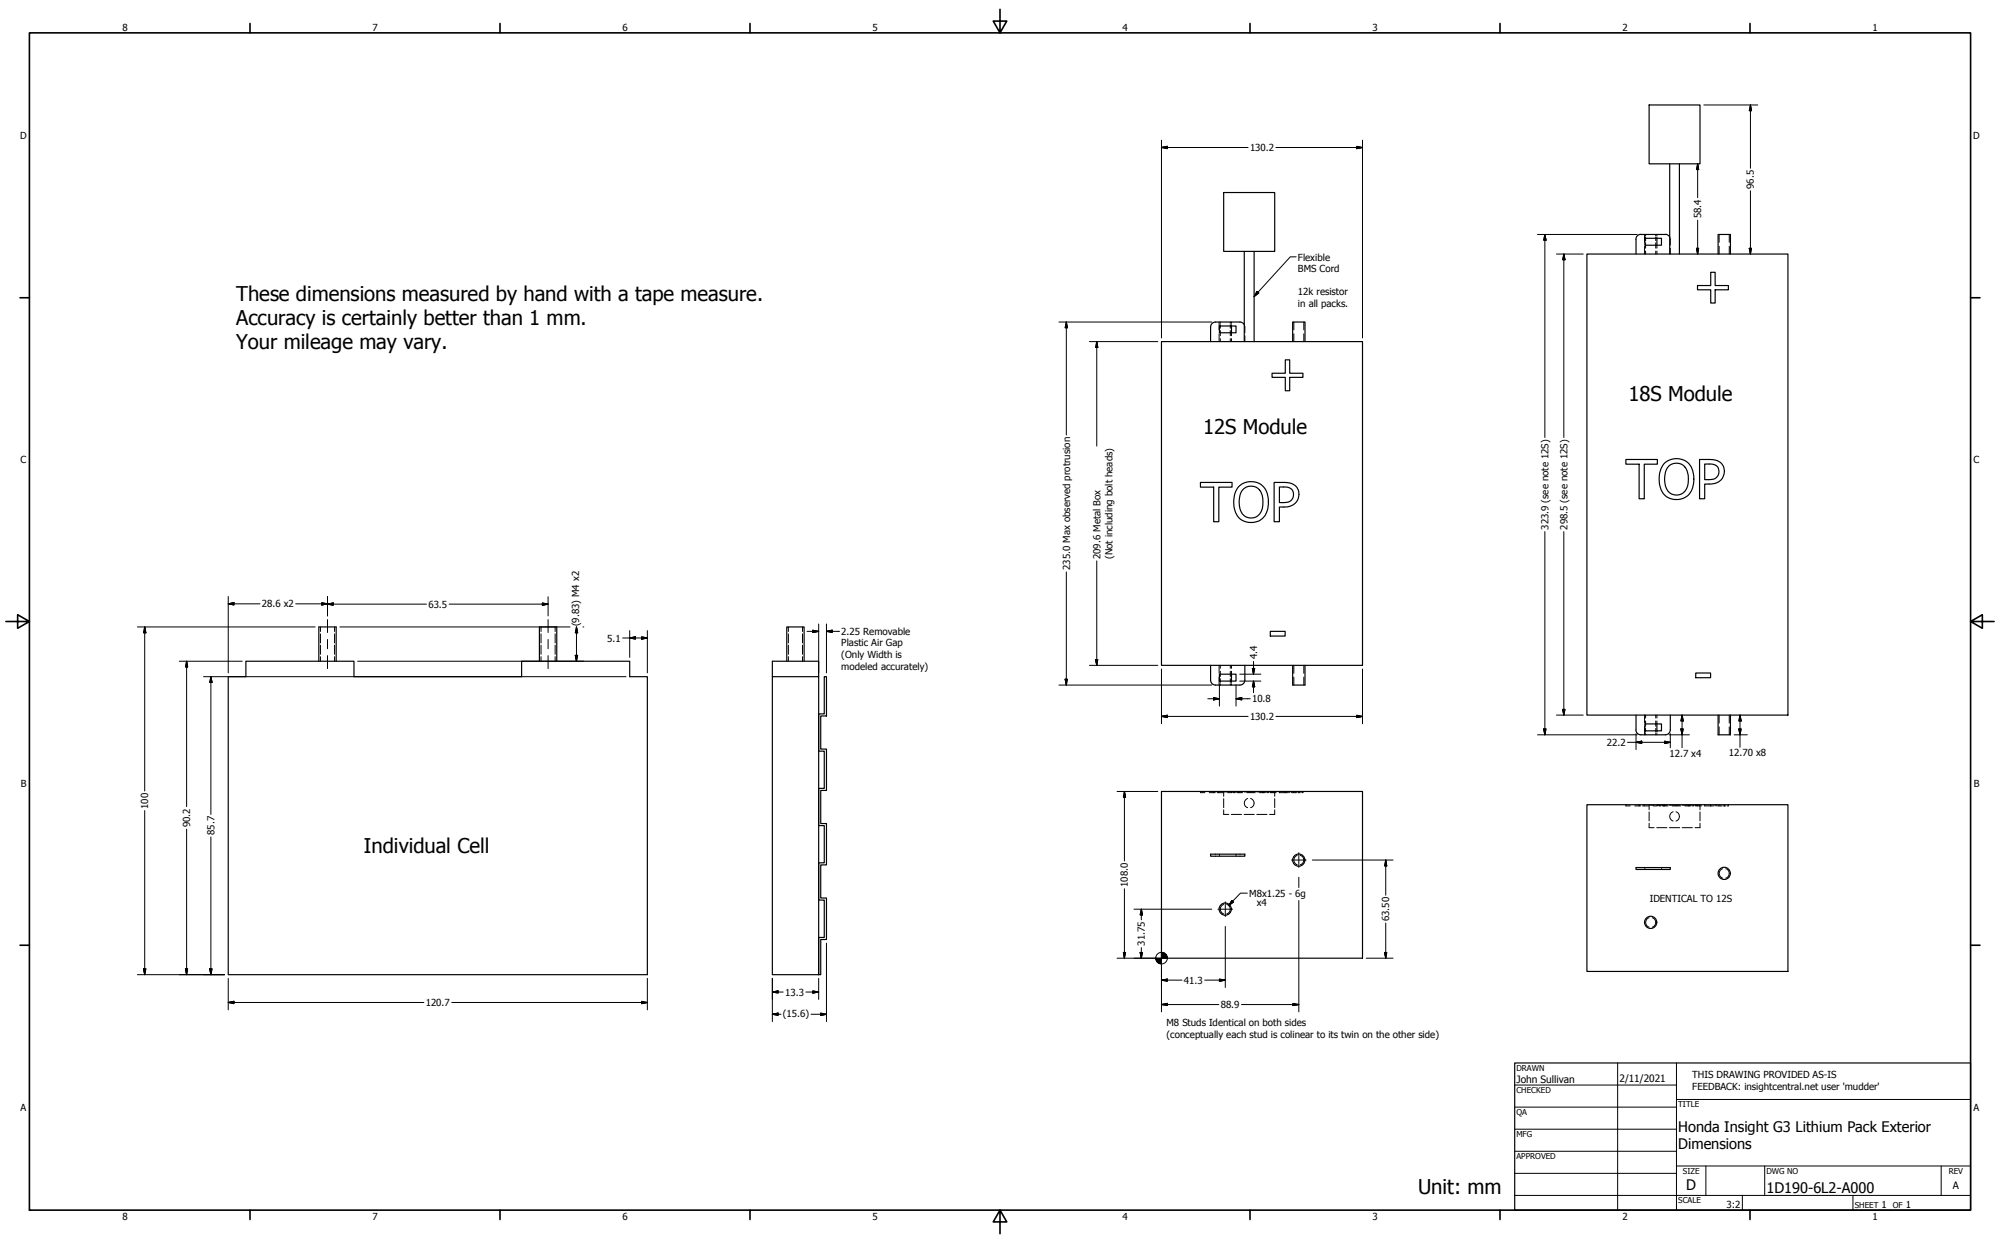
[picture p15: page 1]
SHEET 1 OF 1; DRAWN; CHECKED; MFG; APPROVED; John Sullivan; DWG NO 1D190-6L2-A000; SIZE D; SCALE; REV A; Individual Cell; 12S Module; 18S Module; etal B; clu; din; olt h; erv; protru; sio; IDENTICAL TO 12S; Flexible BMS Cord; Unit: mm; ote 12

12k resistor
in all packs.

Accuracy is certainly better than 1 mm.
Your mileage may vary.

2.25 Removable
Plastic Air Gap
(Only Width is
modeled accurately)

M8 Studs Identical on both sides
(conceptually each stud is colinear to its twin on the other side)

THIS DRAWING PROVIDED AS-IS
FEEDBACK: insightcentral.net user 'mudder'

TITLE
Honda Insight G3 Lithium Pack Exterior
Dimensions

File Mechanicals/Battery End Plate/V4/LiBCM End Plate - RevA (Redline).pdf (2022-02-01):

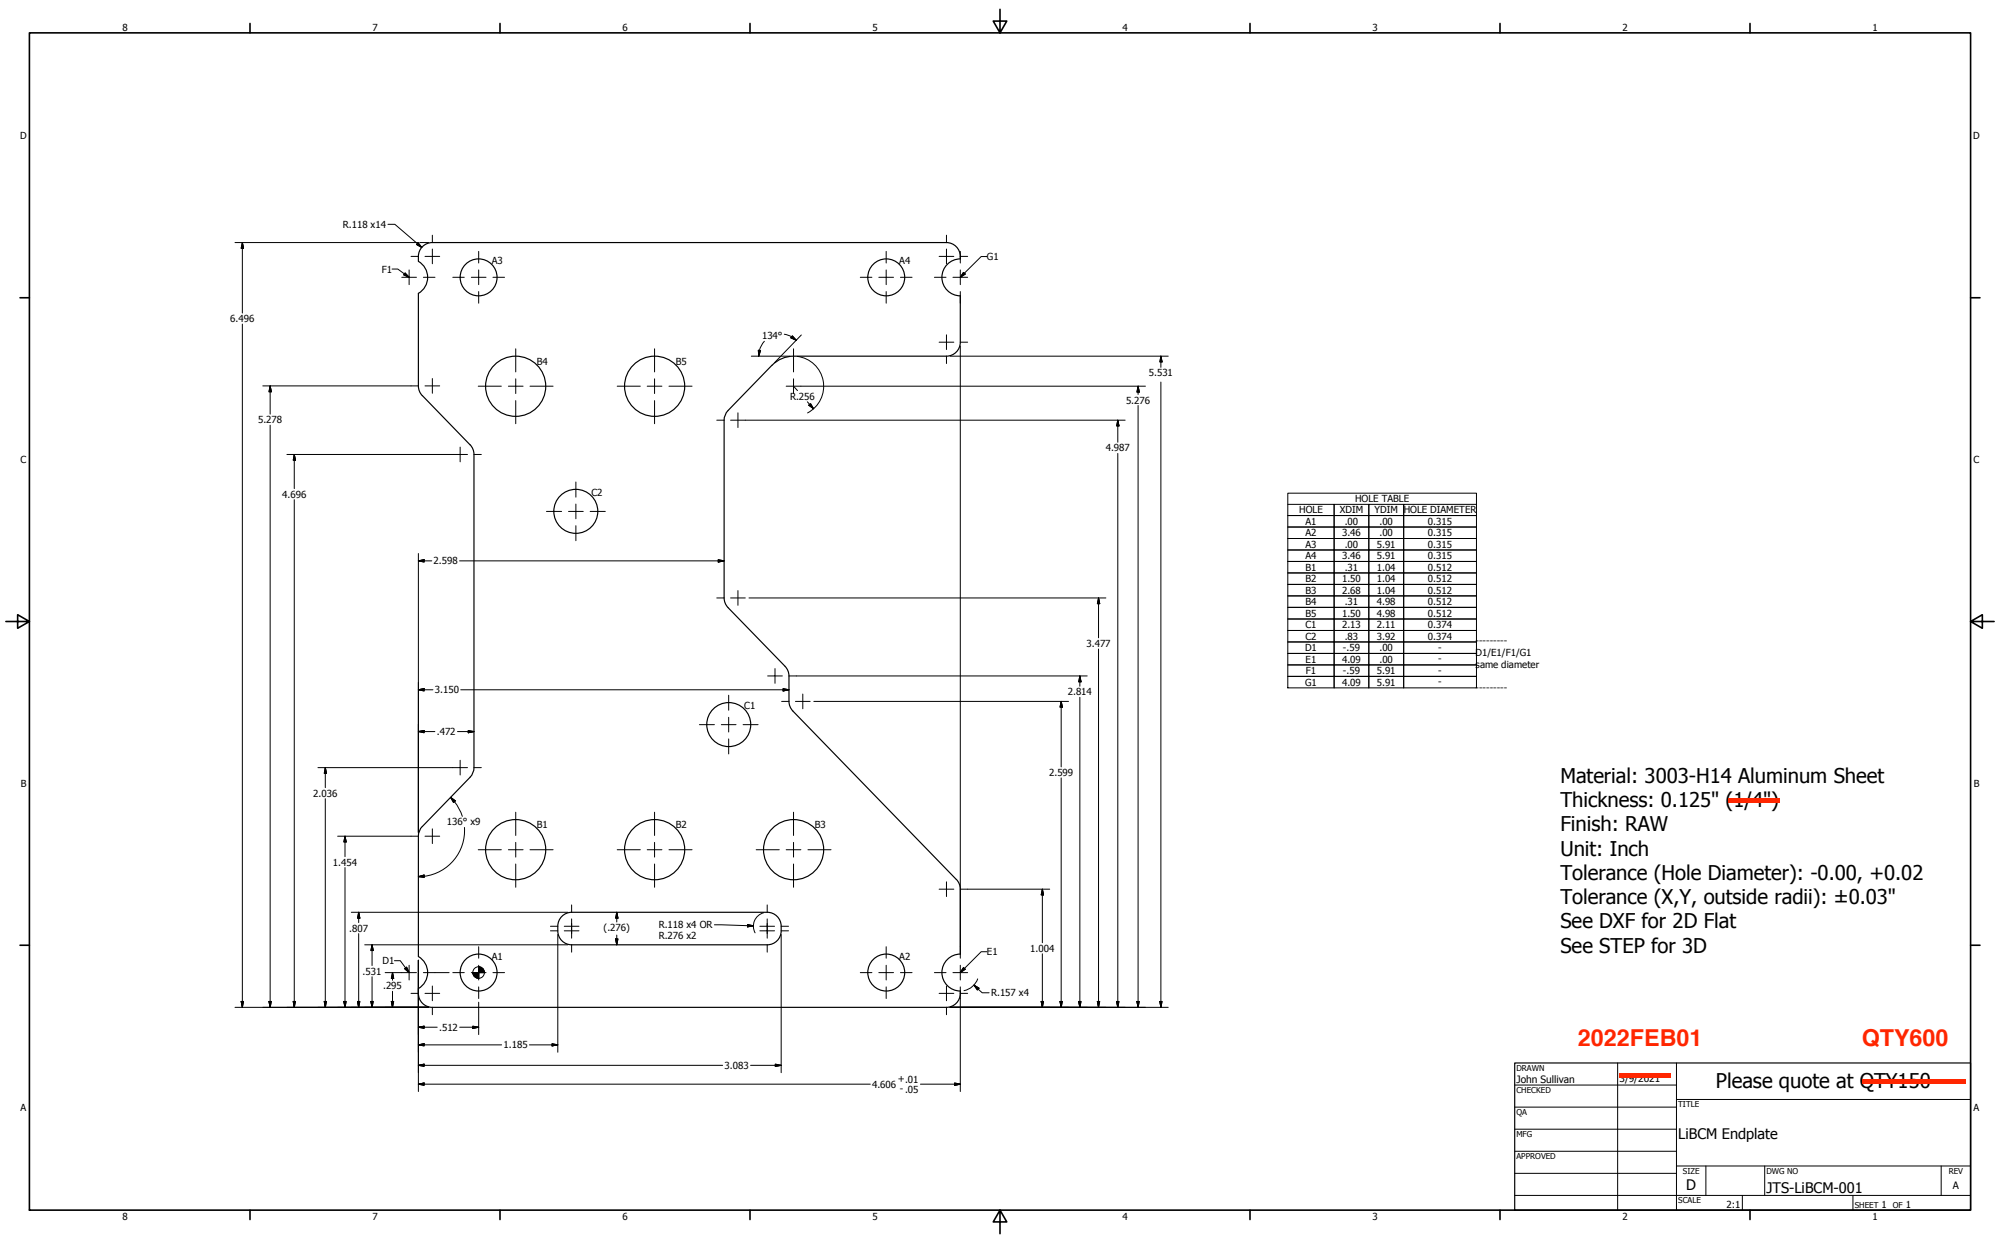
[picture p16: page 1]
SHEET 1 OF 1; DRAWN; CHECKED; MFG; APPROVED; John Sullivan; DWG NO JTS-LiBCM-001; TITLE; LiBCM Endplate; SIZE D; SCALE; REV A; HOLE TABLE; HOLE; XDIM YDIM HOLE DIAMETER; --------- D1/E1/F1/G1 same diameter

Material: 3003-H14 Aluminum Sheet
Thickness: 0.125" (1/4")
Finish: RAW
Unit: Inch
Tolerance (Hole Diameter): -0.00, +0.02
Tolerance (X,Y, outside radii): ±0.03"
See DXF for 2D Flat
See STEP for 3D

Please quote at QTY150

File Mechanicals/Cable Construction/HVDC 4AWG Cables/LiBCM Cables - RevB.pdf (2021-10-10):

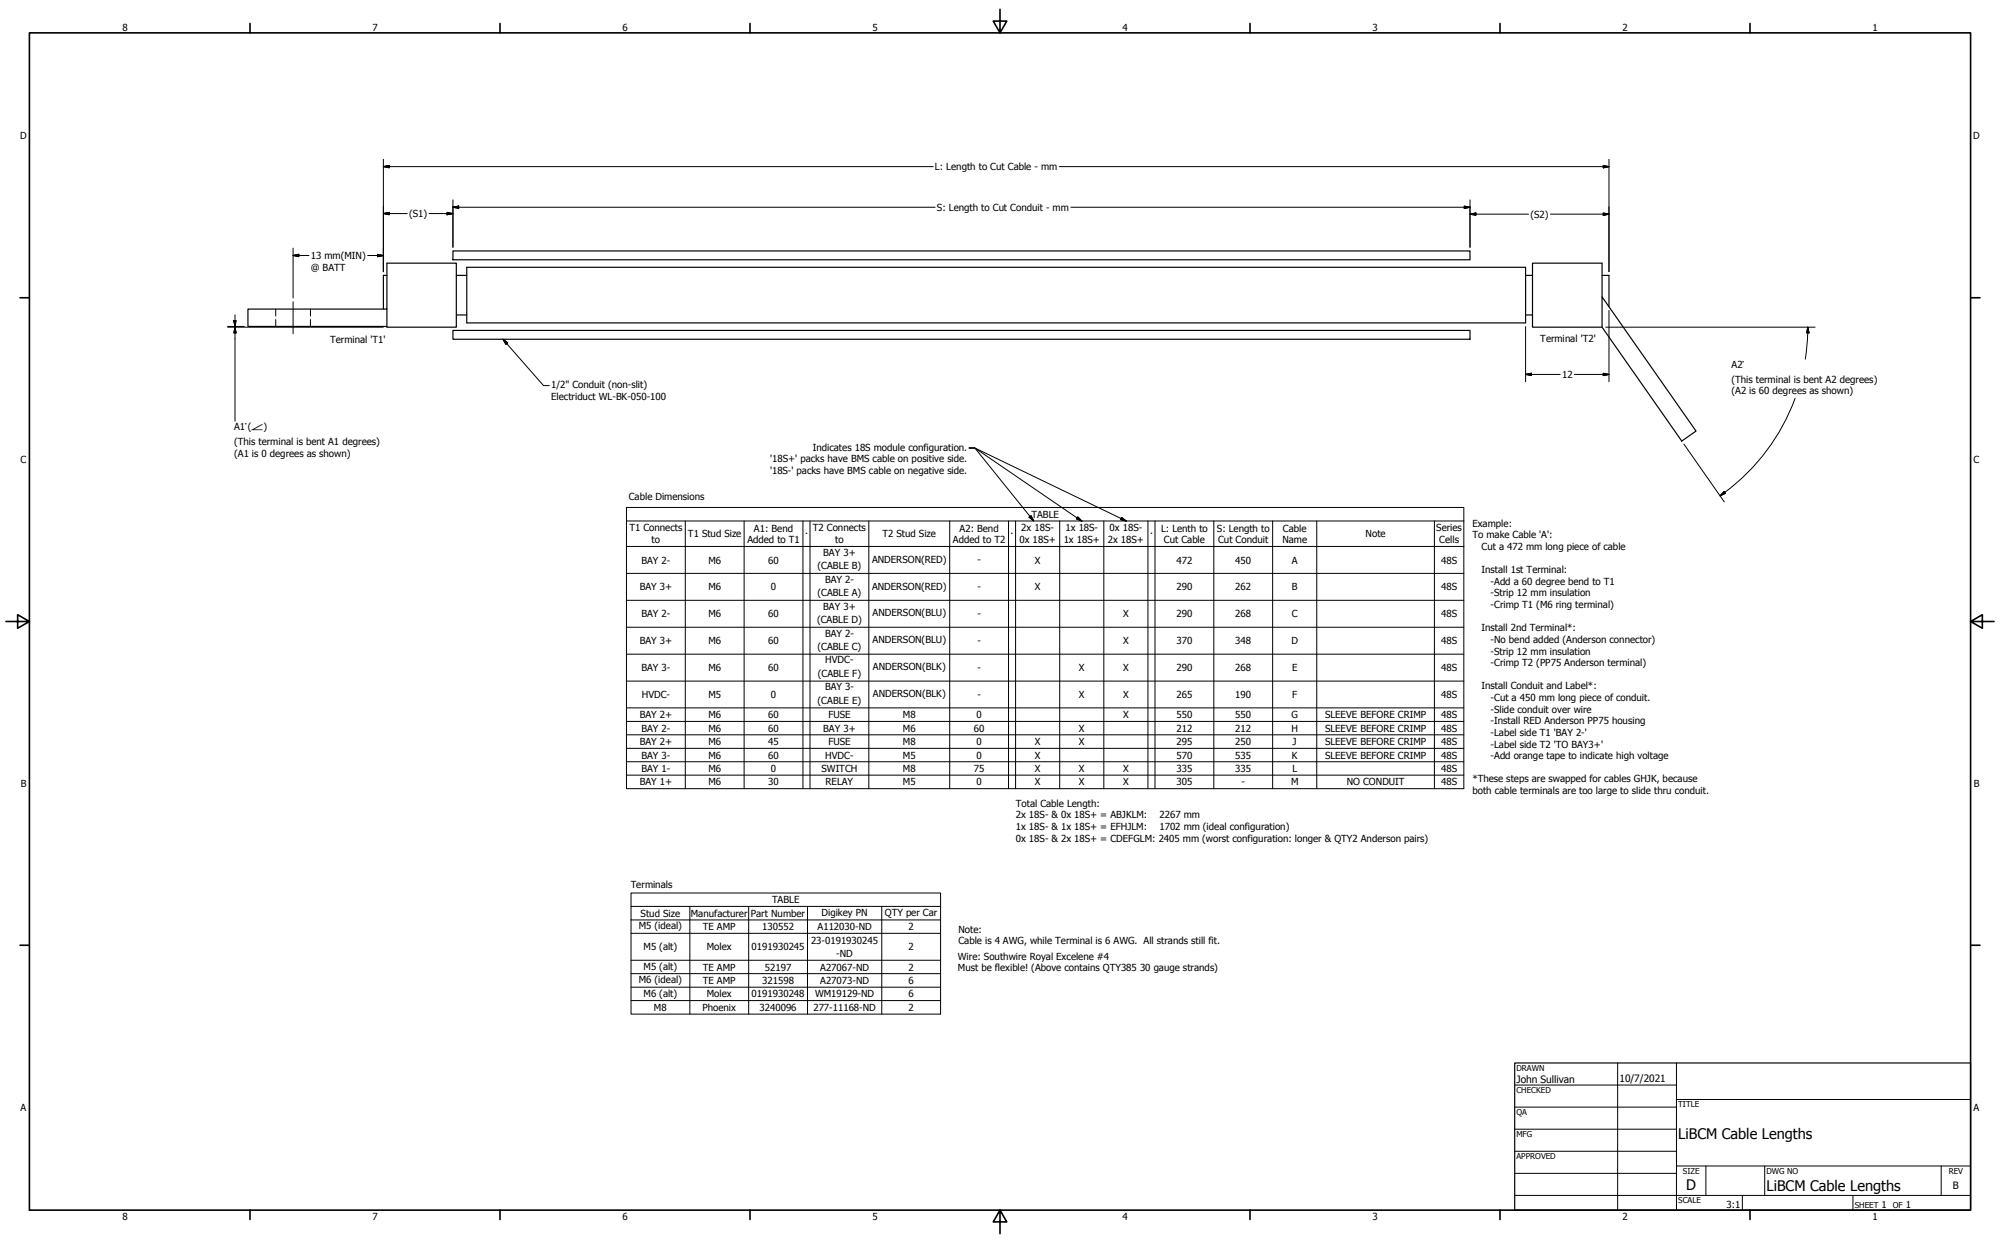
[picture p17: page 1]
SHEET 1 OF 1; DRAWN; CHECKED; MFG; APPROVED; John Sullivan; SIZE D; SCALE; REV B; Terminal 'T1'; TABLE; T1 Connects to; T1 Stud Size; A1: Bend Added to T1; T2 Connects to; T2 Stud Size; A2: Bend Added to T2; L: Lenth to Cut Cable; S: Length to Cut Conduit; Cable Name; Note; Series Cells; BAY 2-; BAY 3+ (CABLE B); ANDERSON(RED); BAY 3+; BAY 2- (CABLE A); BAY 3+ (CABLE D); ANDERSON(BLU); BAY 2- (CABLE C); BAY 3-; HVDC- (CABLE F); ANDERSON(BLK); HVDC-; BAY 3- (CABLE E); BAY 2+; FUSE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

L: Length to Cut Cable - mm

S: Length to Cut Conduit - mm

(This terminal is bent A2 degrees)
(A2 is 60 degrees as shown)

1/2" Conduit (non-slit)
Electriduct WL-BK-050-100

(This terminal is bent A1 degrees)
(A1 is 0 degrees as shown)

Indicates 18S module configuration.

'18S+' packs have BMS cable on positive side.
'18S-' packs have BMS cable on negative side.

Example:
To make Cable 'A':
Cut a 472 mm long piece of cable

Install 1st Terminal:
-Add a 60 degree bend to T1
-Strip 12 mm insulation
-Crimp T1 (M6 ring terminal)

Install 2nd Terminal*:
-No bend added (Anderson connector)
-Crimp T2 (PP75 Anderson terminal)

Install Conduit and Label*:
-Cut a 450 mm long piece of conduit.
-Slide conduit over wire
-Install RED Anderson PP75 housing
-Label side T1 'BAY 2-'
-Label side T2 'TO BAY3+'
-Add orange tape to indicate high voltage

*These steps are swapped for cables GHJK, because
both cable terminals are too large to slide thru conduit.

Total Cable Length:
0x 18S- & 2x 18S+ = CDEFGLM: 2405 mm (worst configuration: longer & QTY2 Anderson pairs)

Note:
Cable is 4 AWG, while Terminal is 6 AWG. All strands still fit.
Wire: Southwire Royal Excelene #4
Must be flexible! (Above contains QTY385 30 gauge strands)

TITLE
LiBCM Cable Lengths

DWG NO

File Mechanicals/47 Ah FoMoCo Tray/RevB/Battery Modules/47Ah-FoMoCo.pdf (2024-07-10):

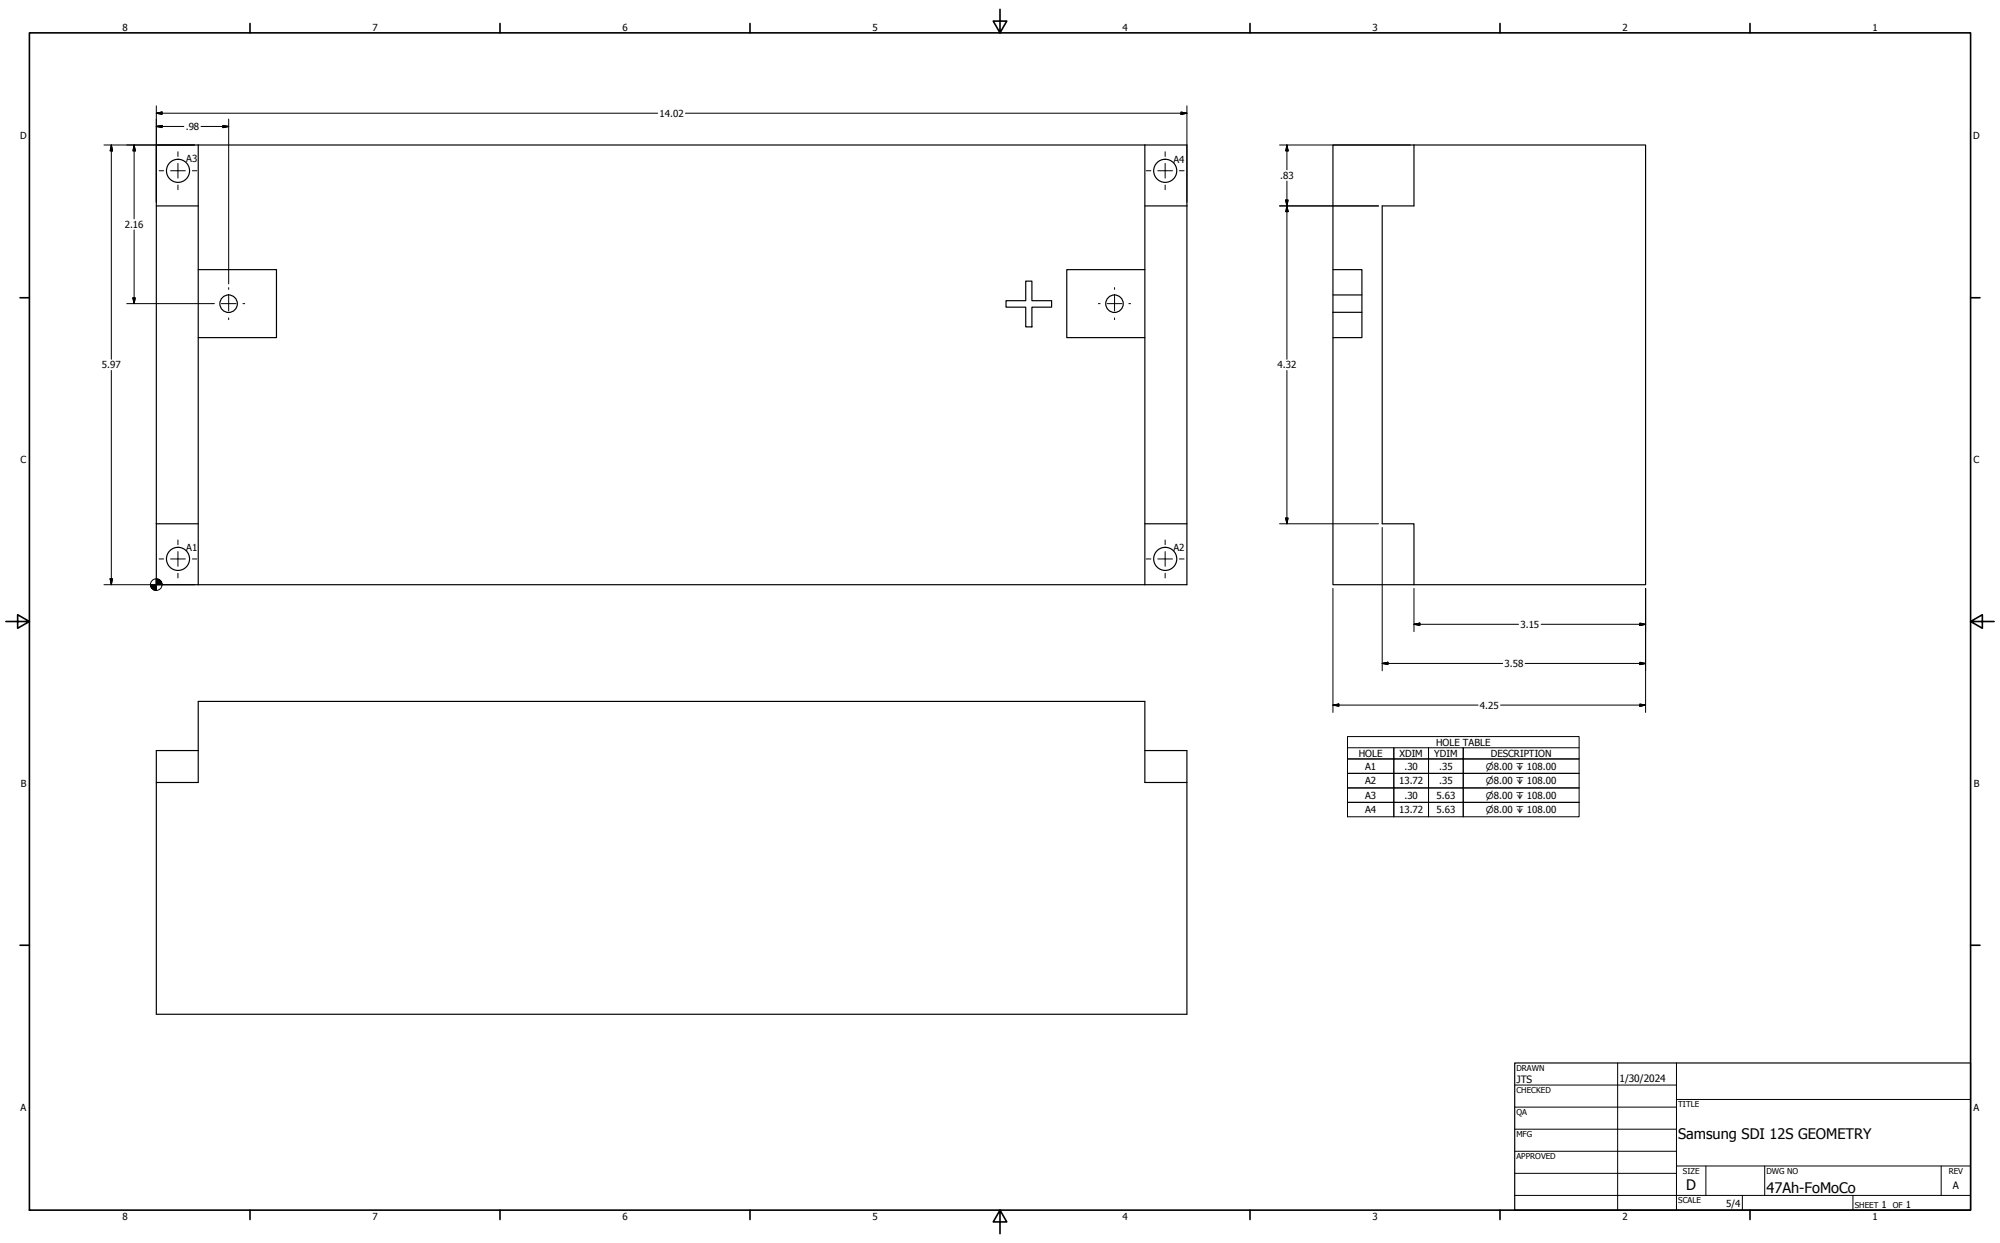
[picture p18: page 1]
SHEET 1 OF 1; DRAWN; CHECKED; MFG; APPROVED; JTS; DWG NO 47Ah-FoMoCo; SIZE D; SCALE; REV A; HOLE TABLE; HOLE; XDIM; YDIM; DESCRIPTION

TITLE
Samsung SDI 12S GEOMETRY

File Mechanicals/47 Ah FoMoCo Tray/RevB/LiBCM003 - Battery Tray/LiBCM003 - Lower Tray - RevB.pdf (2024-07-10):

Verify uniform bend radius.

## QTY5 pieces from previous batch

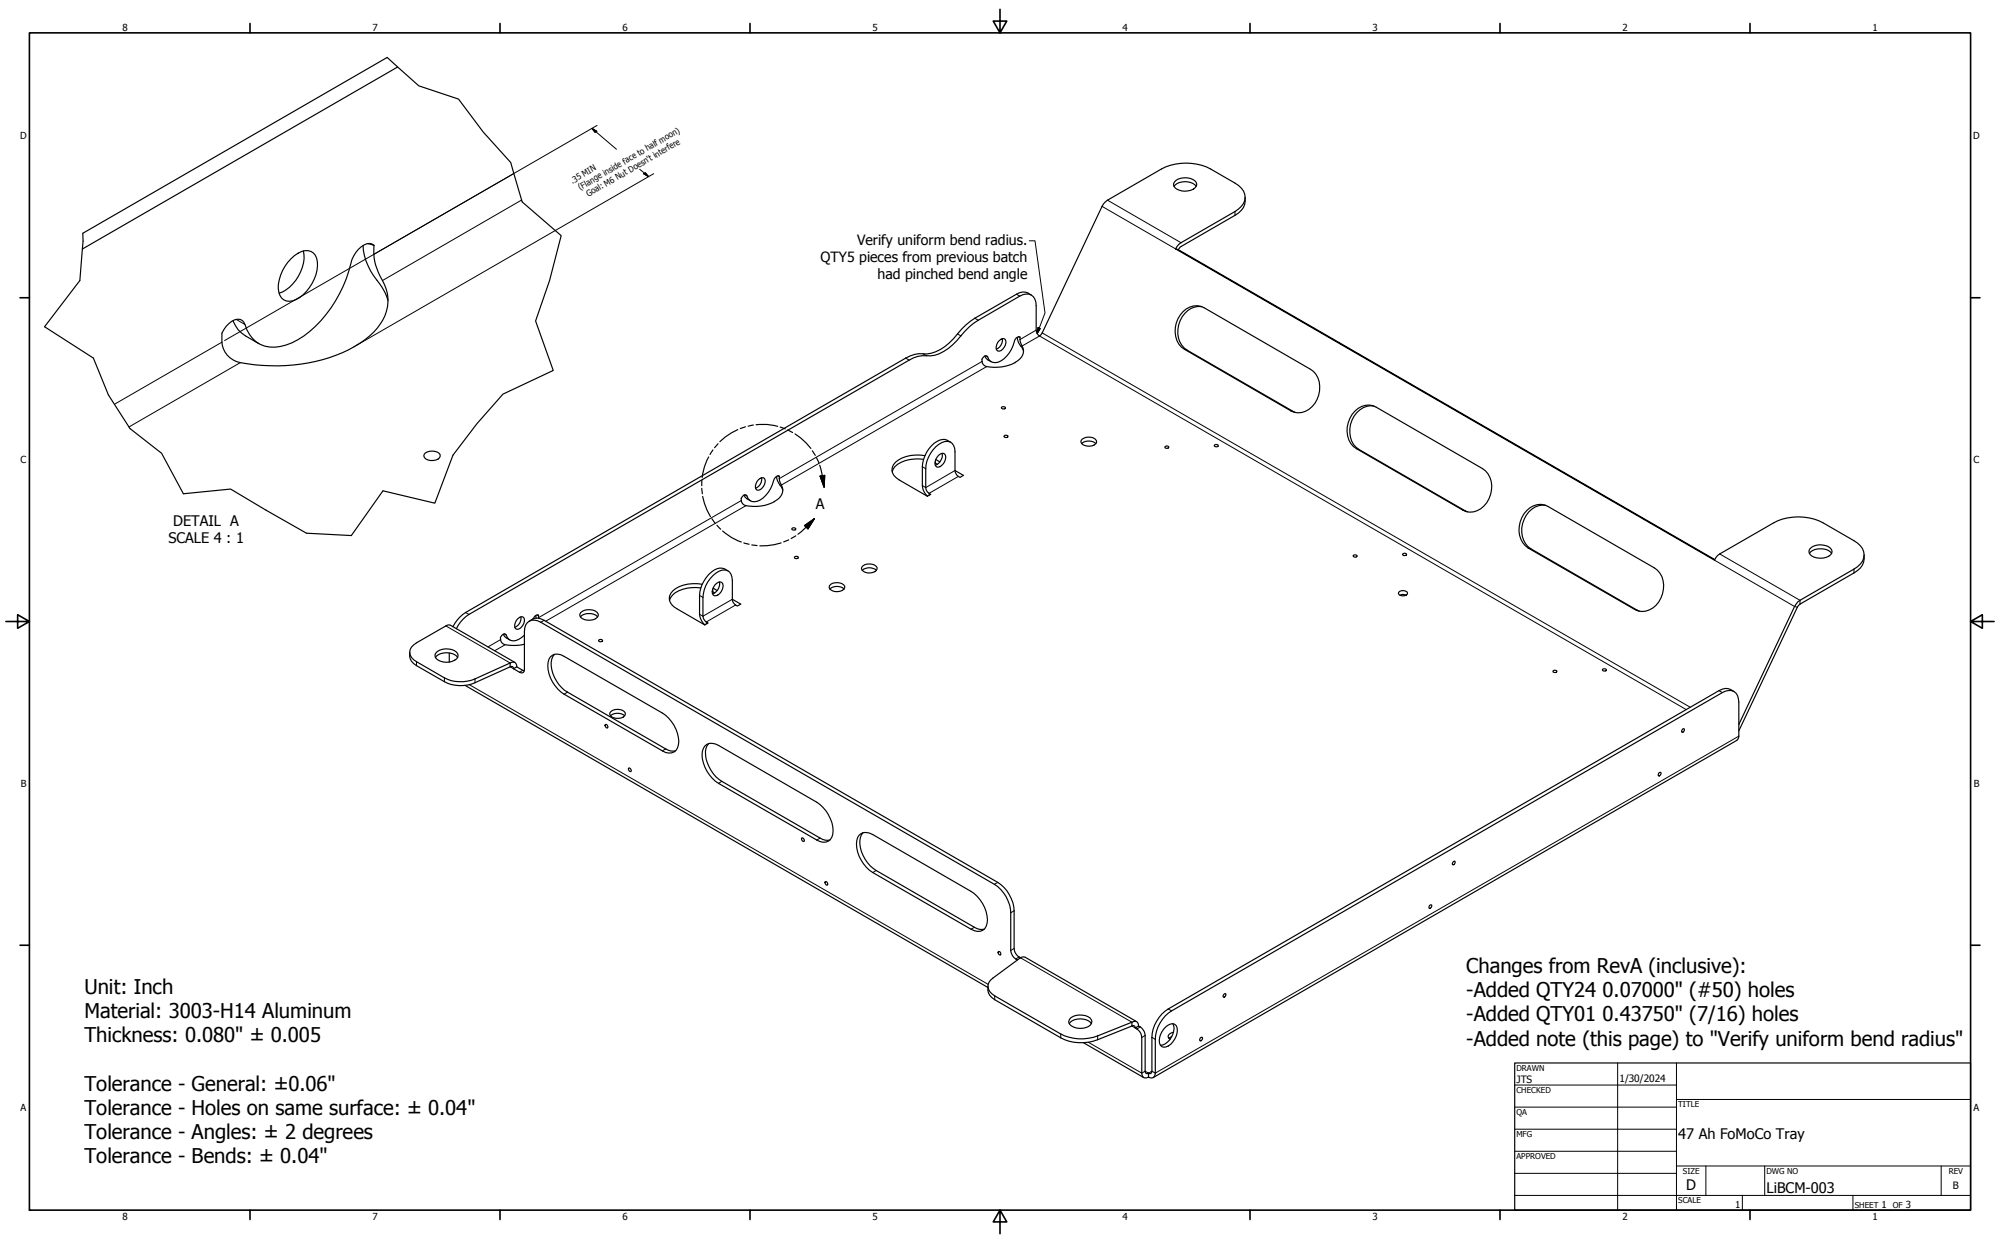
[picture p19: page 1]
DETAIL A SCALE 4 : 1; SHEET 1 OF 3; DRAWN; CHECKED; MFG; APPROVED; JTS; DWG NO LiBCM-003; TITLE; SIZE D; SCALE; REV B; .35 MIN; Unit: Inch Material: 3003-H14 Aluminum Thickness: 0.080" ± 0.005

(Flange inside face to half moon)

Goal: M6 Nut Doesn't interfere

had pinched bend angle

Changes from RevA (inclusive):
-Added QTY24 0.07000" (#50) holes
-Added QTY01 0.43750" (7/16) holes
-Added note (this page) to "Verify uniform bend radius"

Tolerance - General: ±0.06"
Tolerance - Holes on same surface: ± 0.04"
Tolerance - Angles: ± 2 degrees
Tolerance - Bends: ± 0.04"

47 Ah FoMoCo Tray

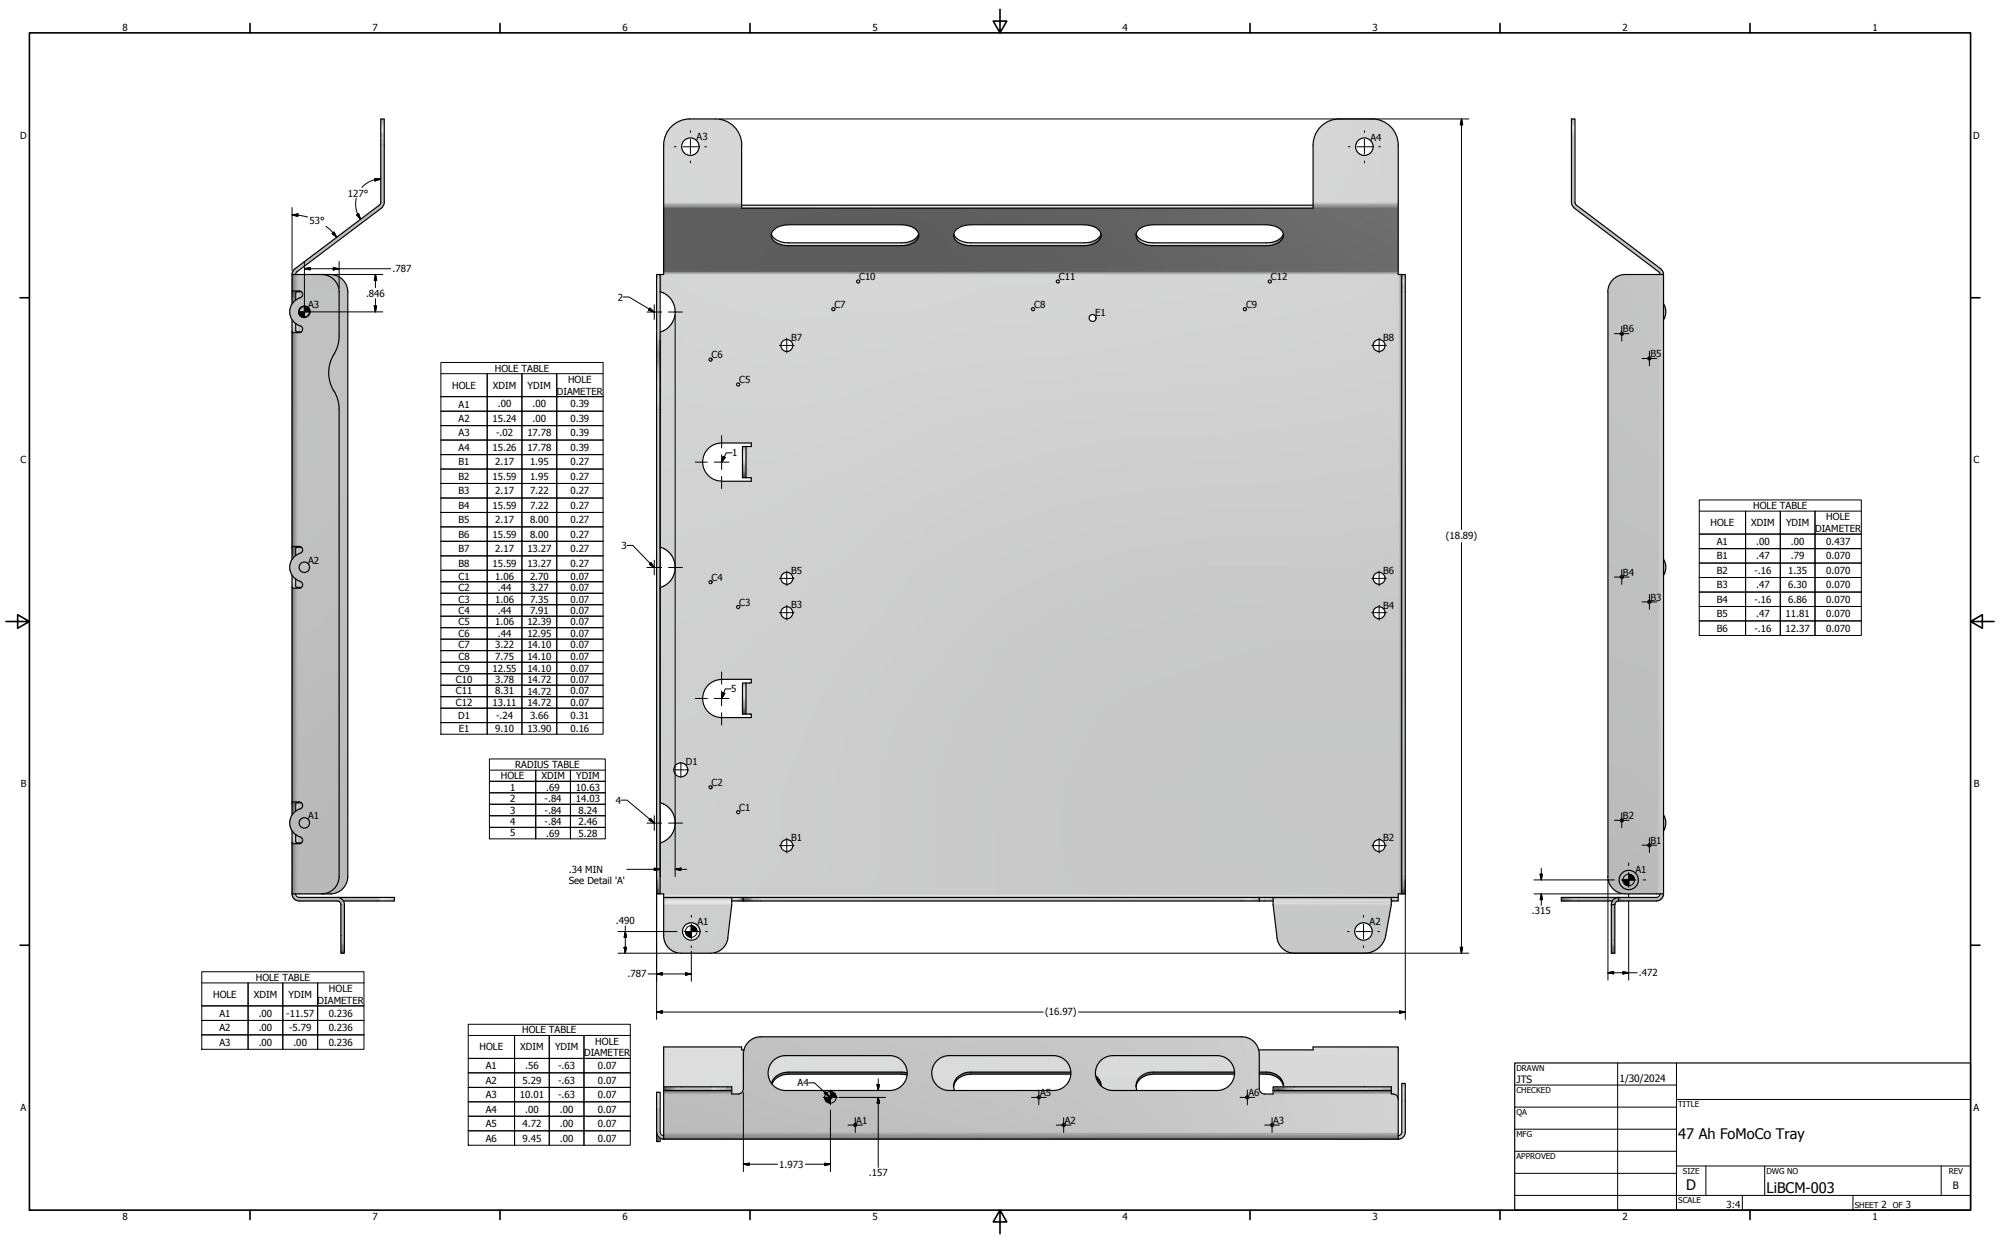
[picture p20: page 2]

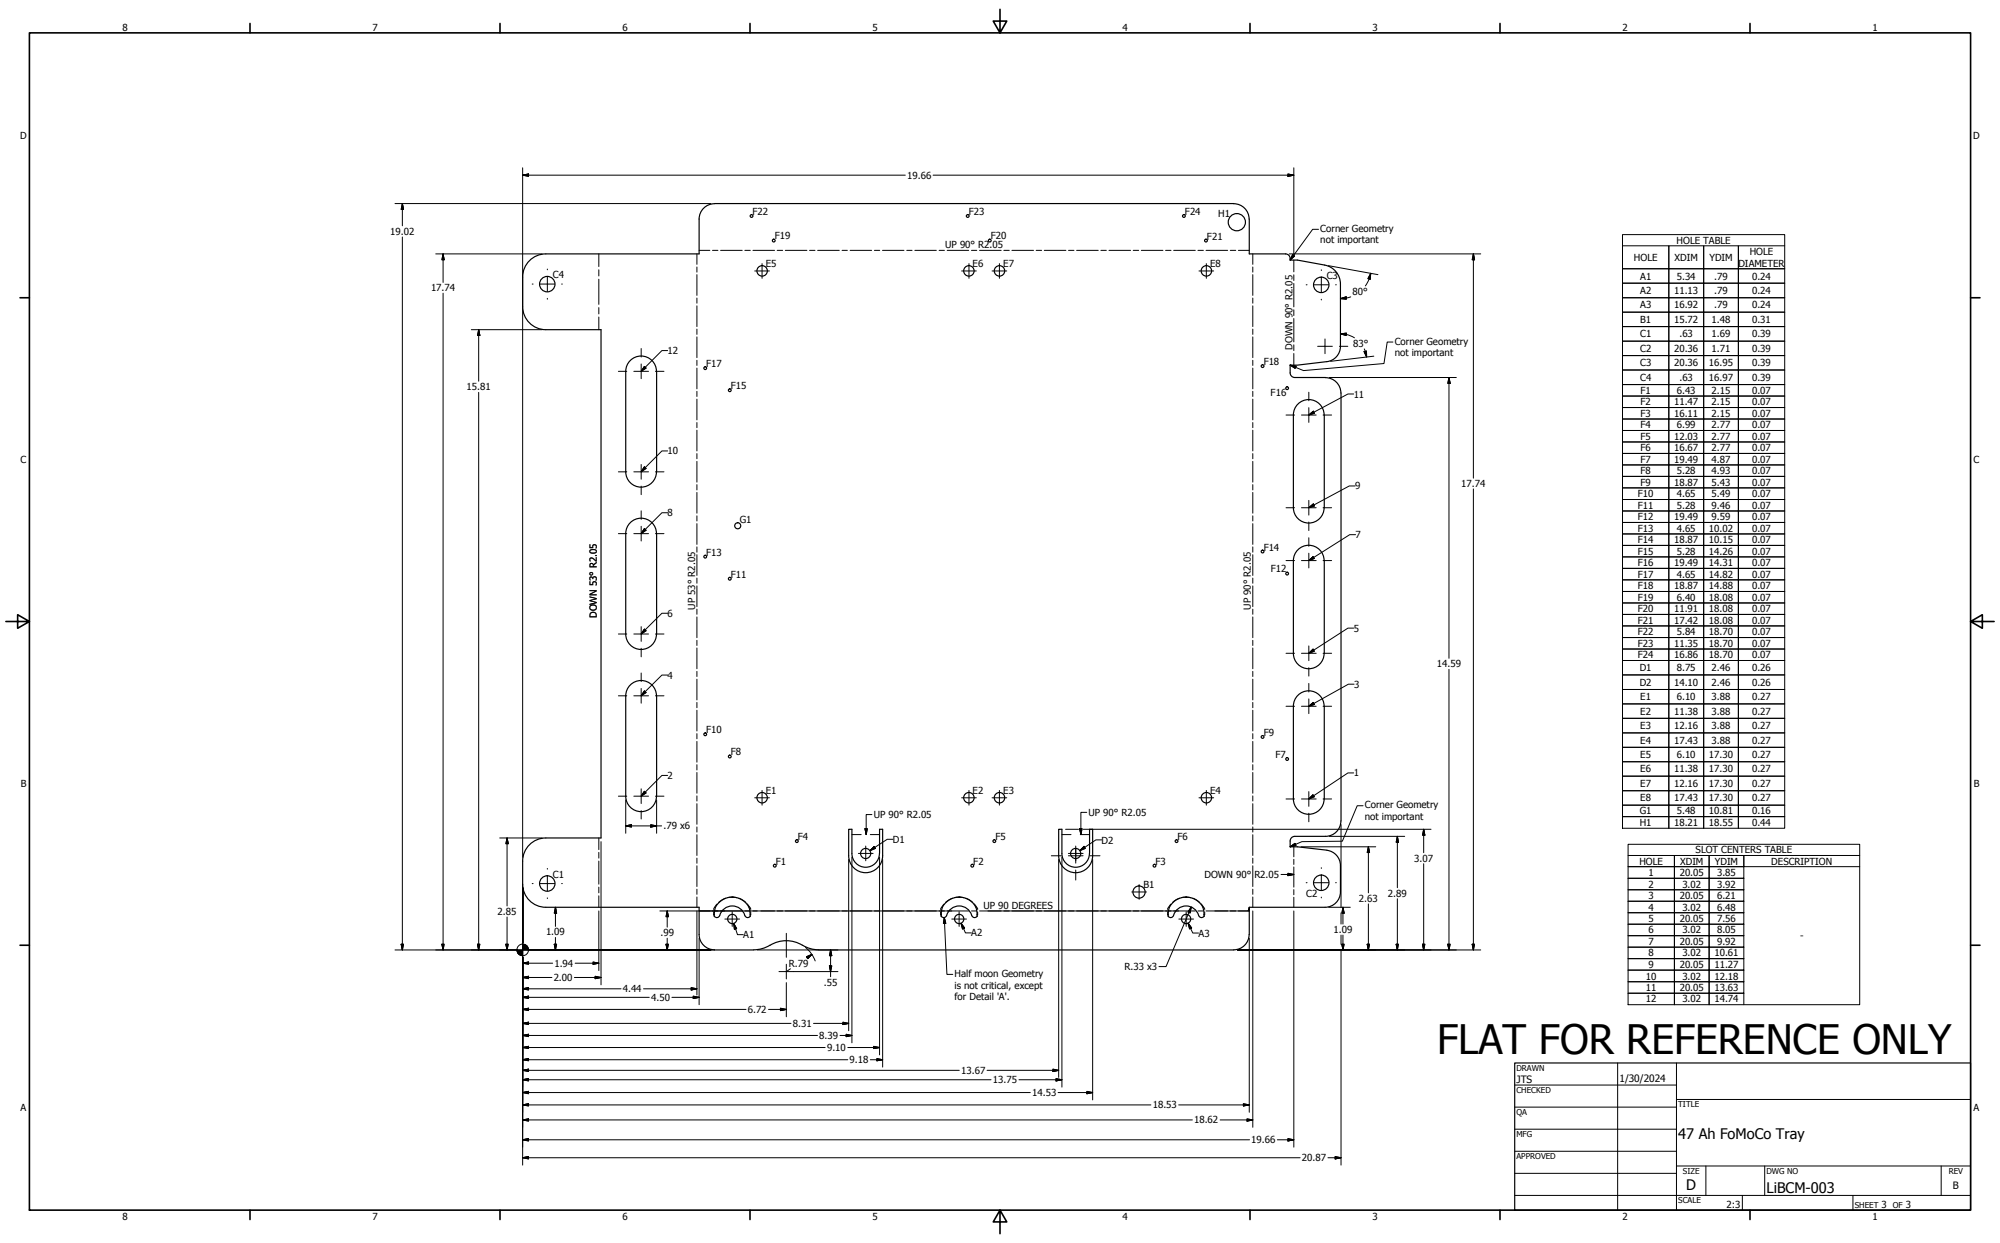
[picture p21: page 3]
alf; DOWN 90° R2.05; DOWN 53° R2.05 DOWN 53° R2.05; LAT

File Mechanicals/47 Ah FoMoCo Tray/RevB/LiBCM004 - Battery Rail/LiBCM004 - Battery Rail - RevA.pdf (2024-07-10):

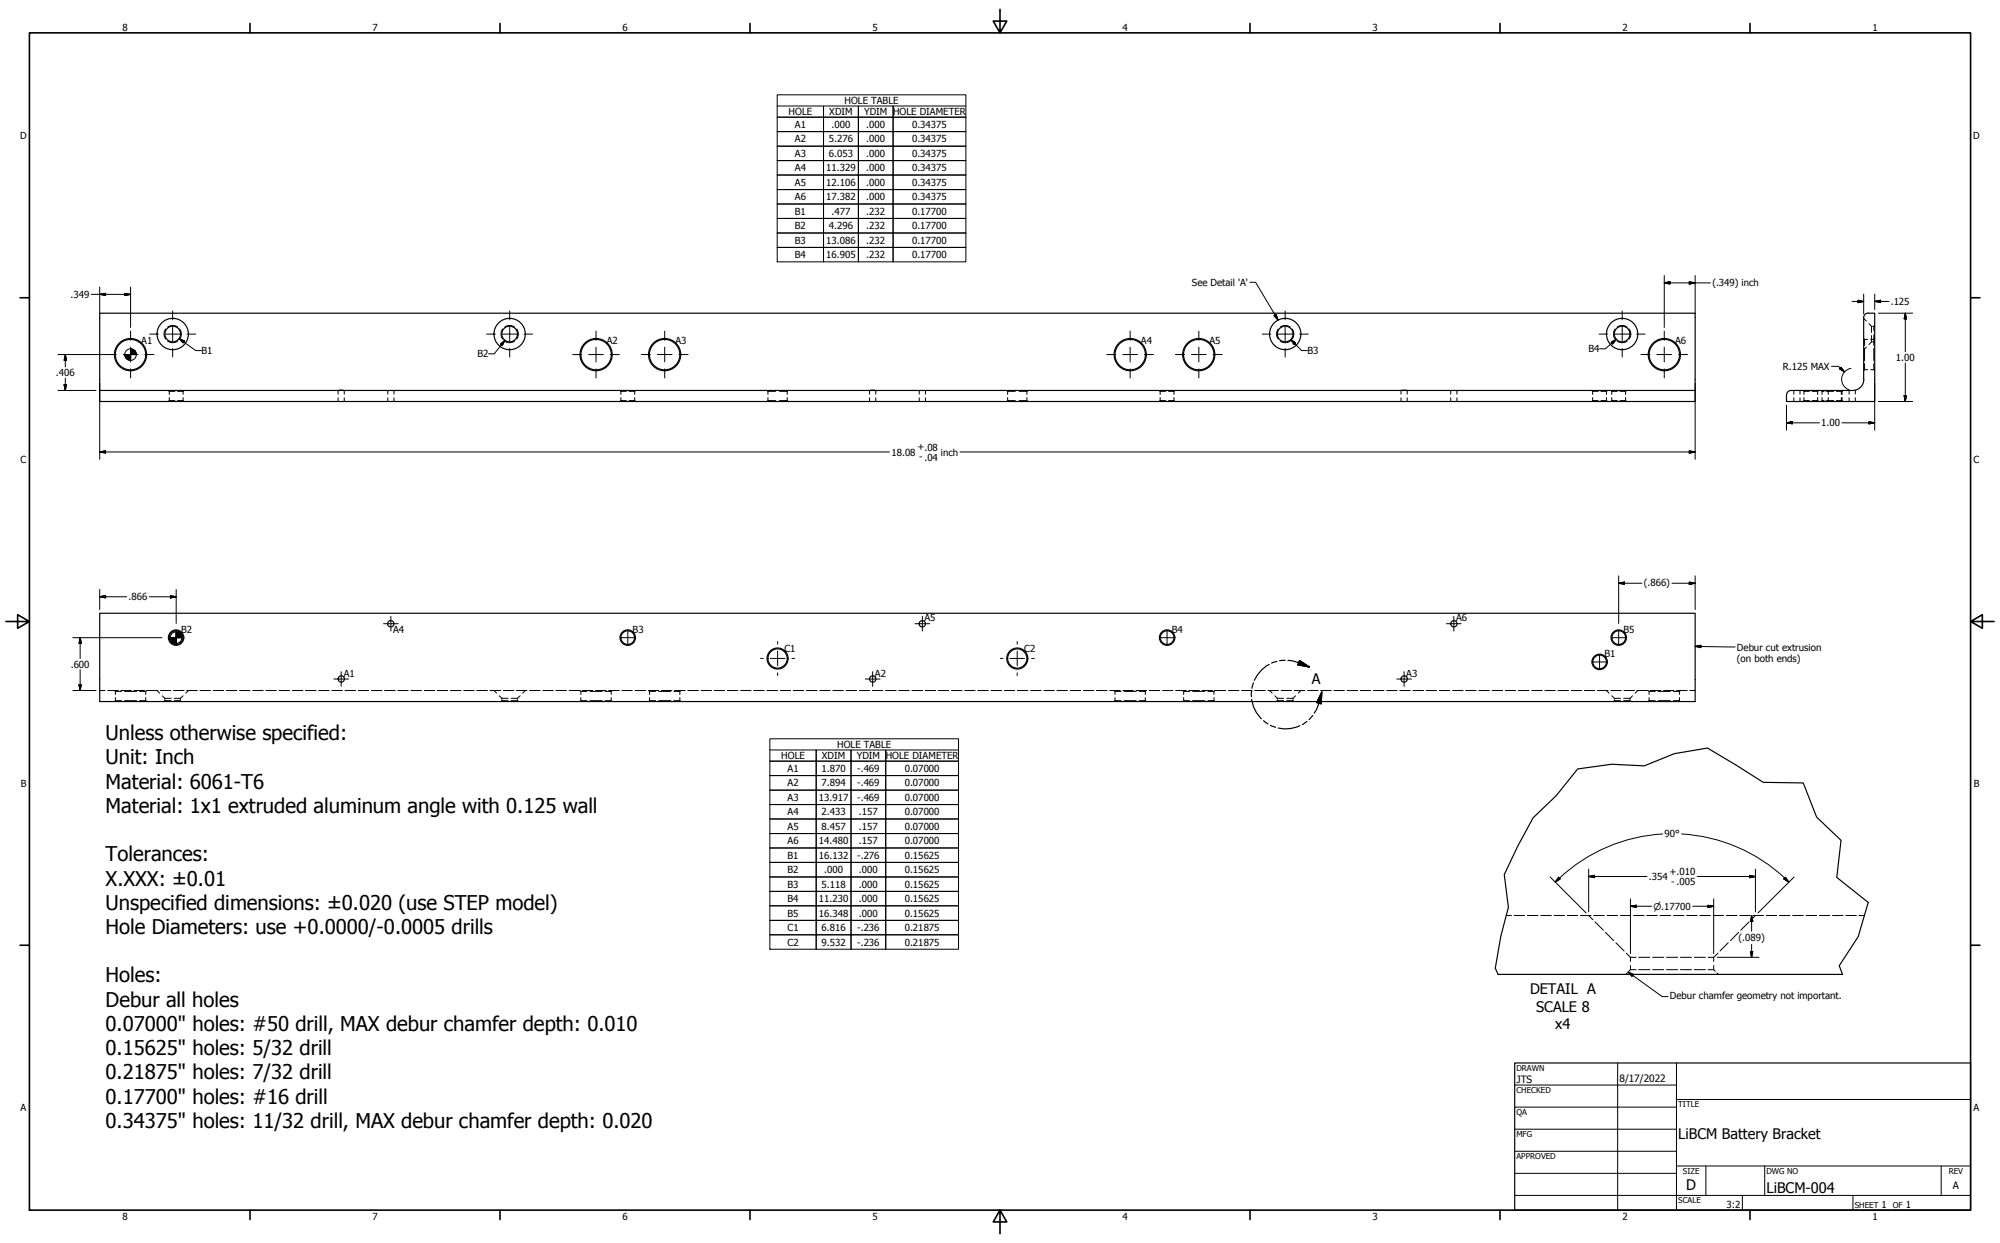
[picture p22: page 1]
DETAIL A SCALE 8 x4; SHEET 1 OF 1; DRAWN; CHECKED; MFG; APPROVED; JTS; DWG NO LiBCM-004; TITLE; SIZE D; SCALE; REV A; inch; R.125 MAX; (.349) inch; HOLE TABLE; HOLE; XDIM; YDIM HOLE DIAMETER; See Detail 'A'

Debur cut extrusion
(on both ends)

Unless otherwise specified:
Unit: Inch
Material: 6061-T6
Material: 1x1 extruded aluminum angle with 0.125 wall

Tolerances:
X.XXX: ±0.01
Unspecified dimensions: ±0.020 (use STEP model)
Hole Diameters: use +0.0000/-0.0005 drills

Holes:
Debur all holes
0.07000" holes: #50 drill, MAX debur chamfer depth: 0.010
0.15625" holes: 5/32 drill
0.21875" holes: 7/32 drill
0.17700" holes: #16 drill
0.34375" holes: 11/32 drill, MAX debur chamfer depth: 0.020

Debur chamfer geometry not important.

LiBCM Battery Bracket

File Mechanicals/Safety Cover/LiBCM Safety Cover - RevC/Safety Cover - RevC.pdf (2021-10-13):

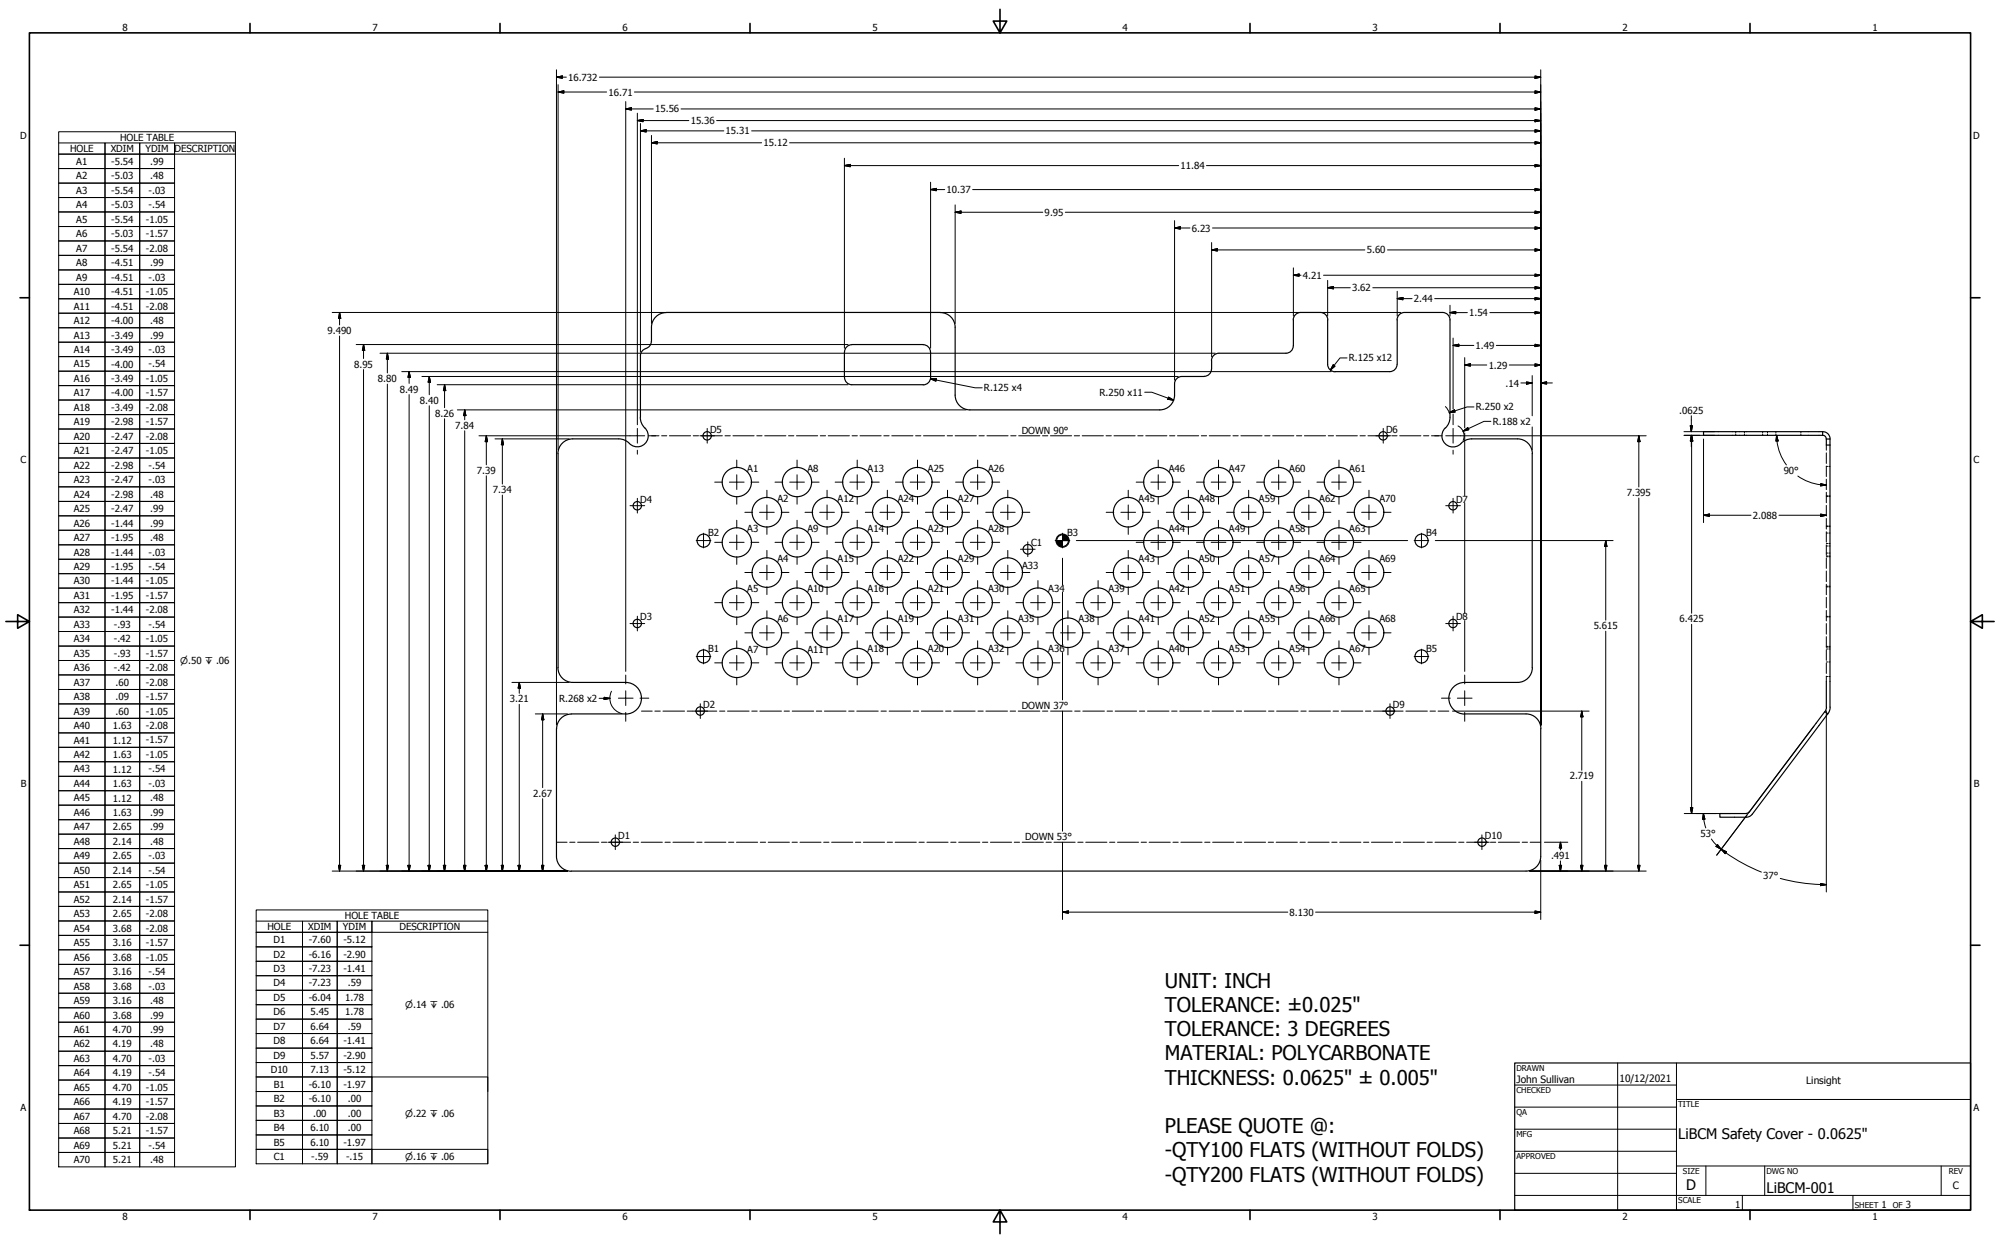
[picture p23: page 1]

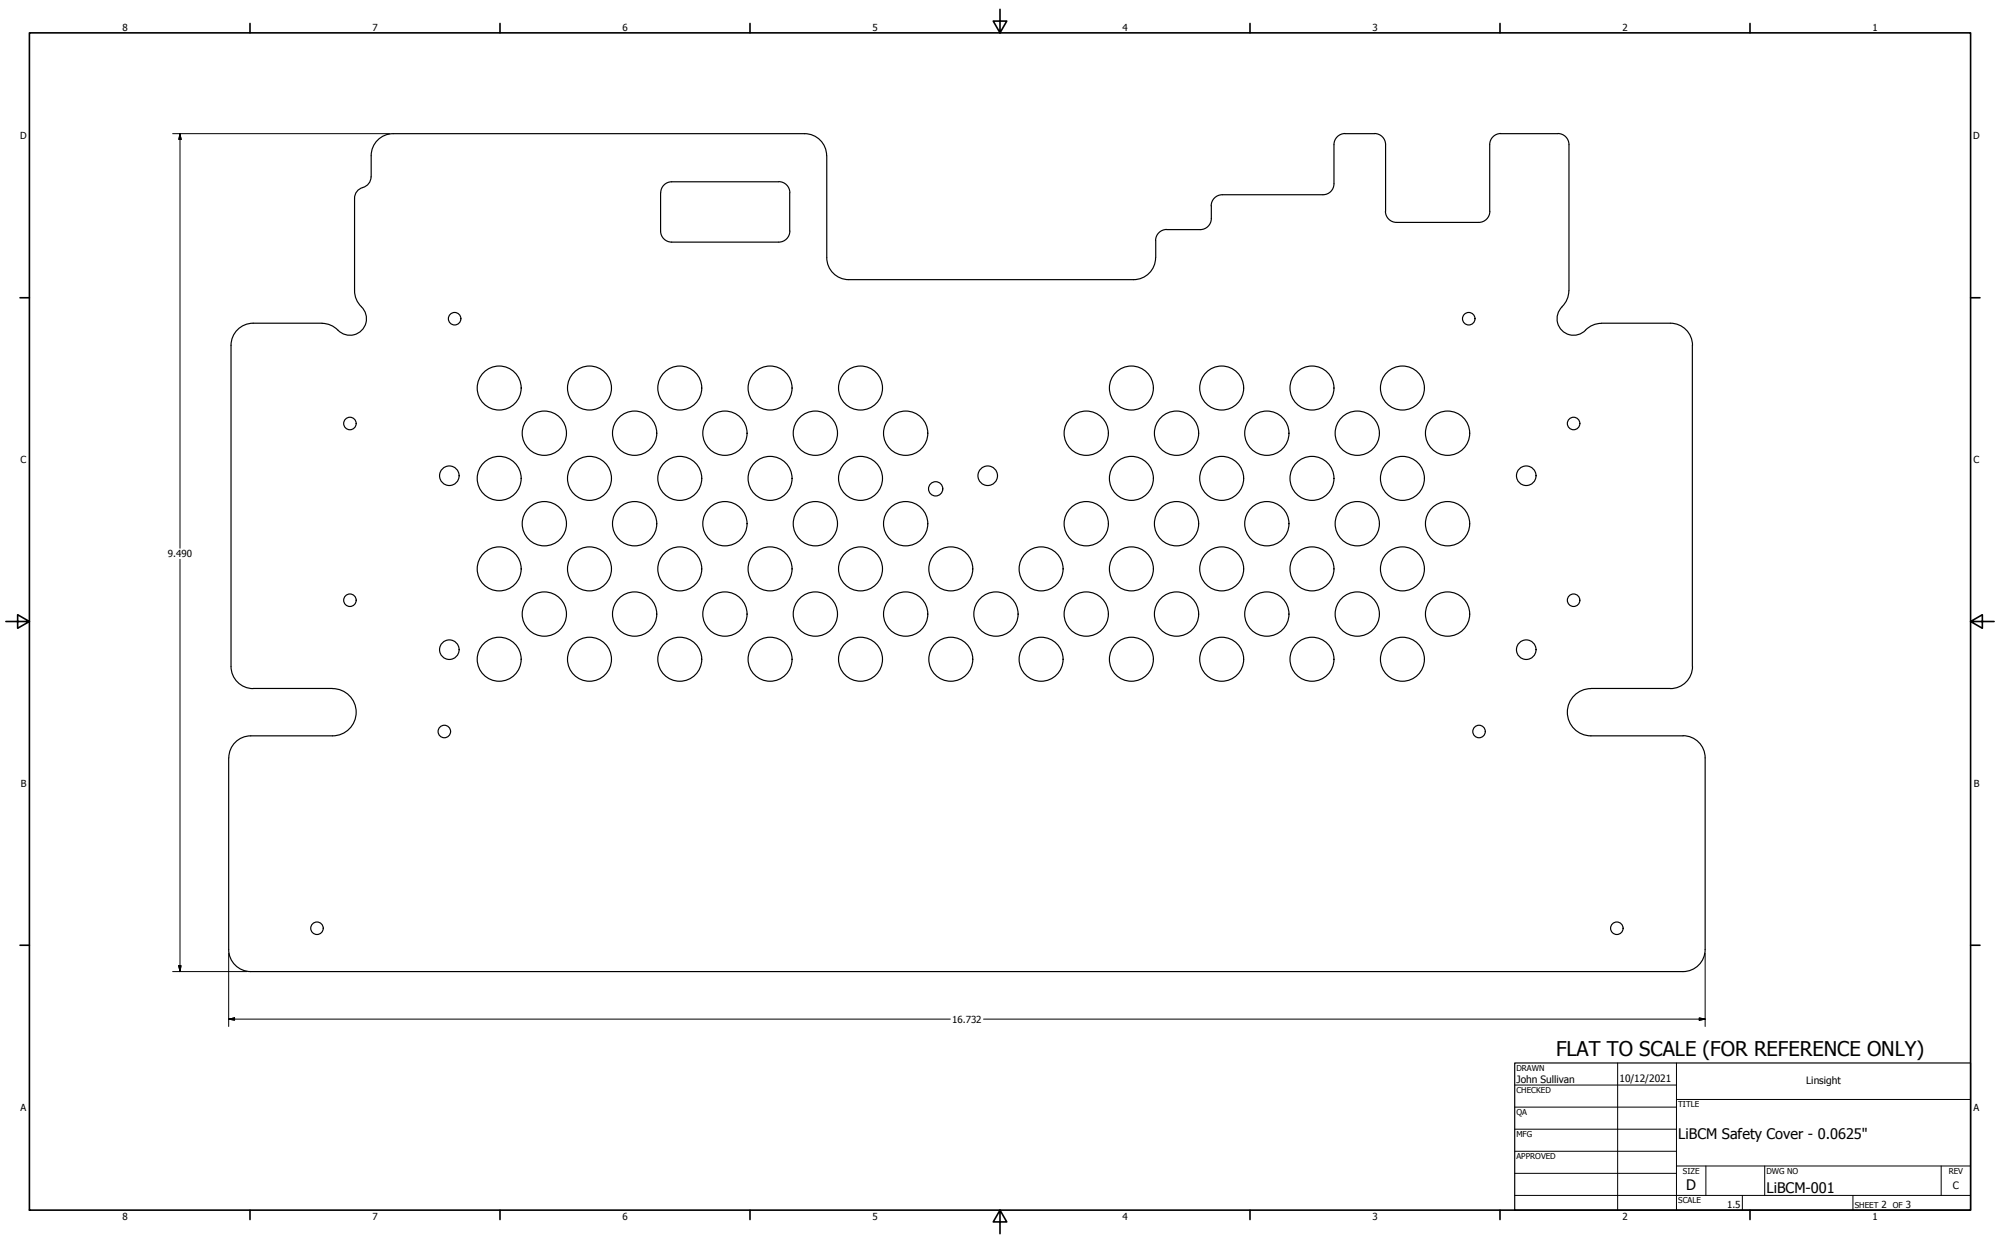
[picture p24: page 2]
SHEET 2 OF 3; DRAWN; CHECKED; MFG; APPROVED; John Sullivan; DWG NO LiBCM-001; TITLE; SIZE D; SCALE; Linsight; REV C

FLAT TO SCALE (FOR REFERENCE ONLY)

LiBCM Safety Cover - 0.0625"

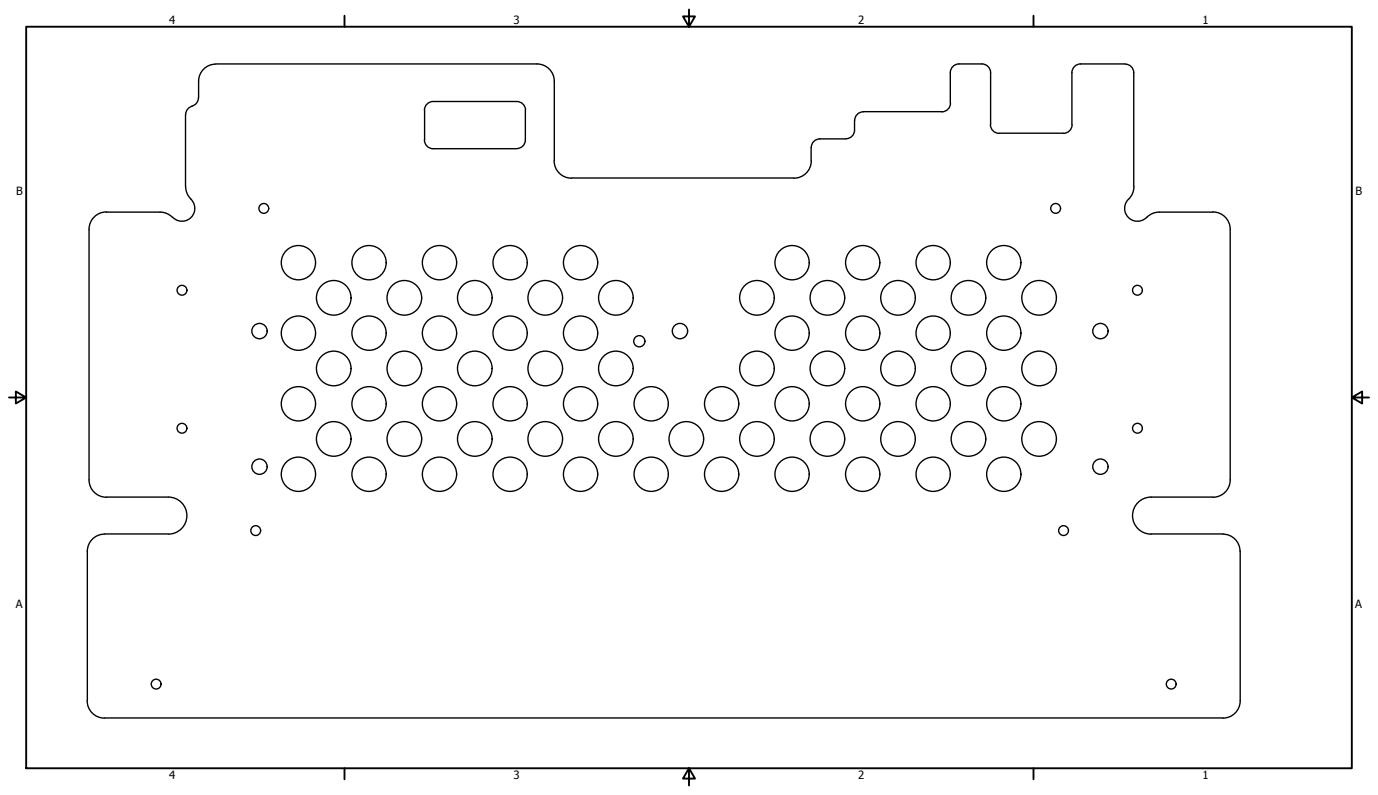
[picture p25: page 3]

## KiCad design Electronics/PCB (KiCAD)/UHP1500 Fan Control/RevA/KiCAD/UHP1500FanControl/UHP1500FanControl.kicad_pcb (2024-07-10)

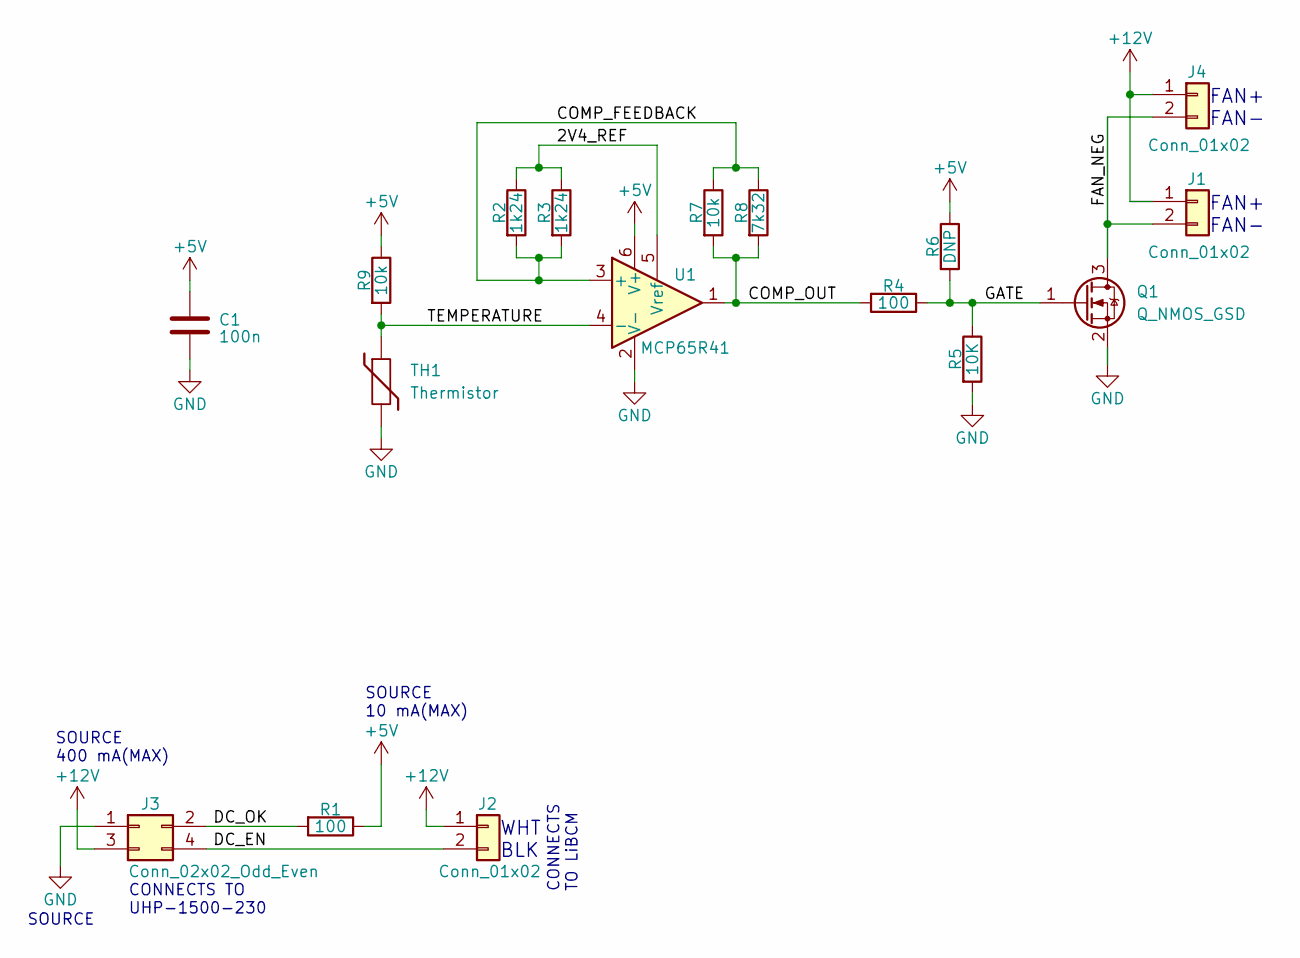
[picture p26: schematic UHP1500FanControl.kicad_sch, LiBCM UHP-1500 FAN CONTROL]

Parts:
C1: 100n; C_0805_2012Metric
J1, J2, J4: Conn_01x02; DIP-4_W8.89mm_SMDSocket_LongPads
J3: Conn_02x02_Odd_Even; PinHeader_2x02_P2.54mm_Vertical
Q1: Q_NMOS_GSD; SOT-23
R1, R4: 100; R_0805_2012Metric
R2, R3: 1k24; R_0805_2012Metric
R5: 10K; R_0805_2012Metric
R6: DNP; R_0805_2012Metric
R7, R9: 10k; R_0805_2012Metric
R8: 7k32; R_0805_2012Metric
TH1: Thermistor; R_0805_2012Metric
U1: MCP65R41; SOT-23-6

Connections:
+5V: C1.1, R1.1, R6.1, R9.1, U1.6 (V+)
+12V: J1.1, J2.1, J3.3, J4.1
/2V4_REF: R2.1, R3.1, U1.5 (Vref)
/COMP_FEEDBACK: R2.2, R3.2, R7.1, R8.1, U1.3 (+)
/COMP_OUT: R4.2, R7.2, R8.2, U1.1
/DC_EN: J2.2, J3.4
/DC_OK: J3.2, R1.2
/FAN_NEG: J1.2, J4.2, Q1.3 (D)
/GATE: Q1.1 (G), R4.1, R5.1, R6.2
/TEMPERATURE: R9.2, TH1.1, U1.4 (-)
GND: C1.2, J3.1, Q1.2 (S), R5.2, TH1.2, U1.2 (V-)

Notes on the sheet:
SOURCE 10 mA(MAX)
FAN+ FAN-
WHT BLK
CONNECTS TO LiBCM
SOURCE
CONNECTS TO UHP-1500-230
SOURCE 400 mA(MAX)

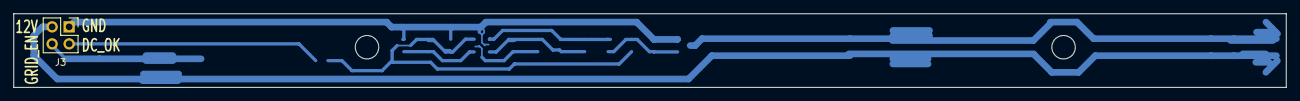
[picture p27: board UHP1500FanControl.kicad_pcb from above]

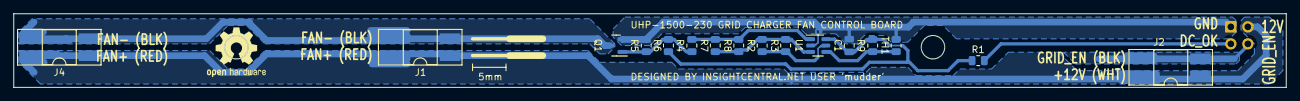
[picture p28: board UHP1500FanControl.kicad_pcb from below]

Board: 2 copper layers, 190.0 x 11.0 mm, 17 parts (16 on the bottom side), 11 nets.

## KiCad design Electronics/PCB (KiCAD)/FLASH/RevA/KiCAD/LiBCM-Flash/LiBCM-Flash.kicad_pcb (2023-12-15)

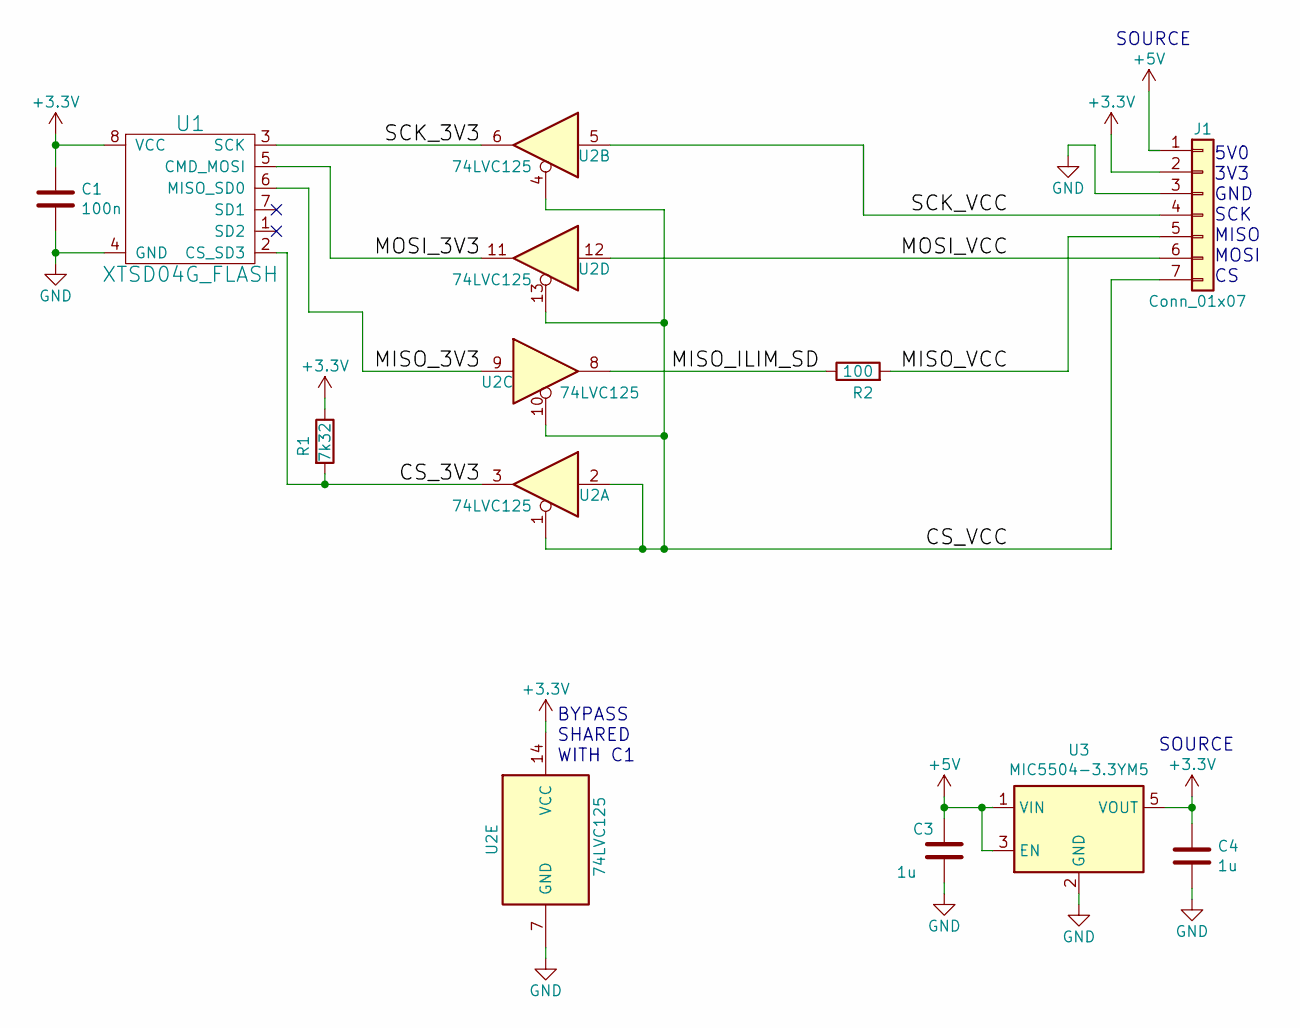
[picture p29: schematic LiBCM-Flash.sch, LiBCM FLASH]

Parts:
C1: 100n; C_0805_2012Metric
C3, C4: 1u; C_0805_2012Metric
J1: Conn_01x07; PinHeader_1x07_P2.54mm_Vertical
R1: 7k32; R_0805_2012Metric
R2: 100; R_0805_2012Metric
U1: XTSD04G_FLASH; NXP_LGA-8_3x5mm_P1.25mm_H1.2mm
U2: 74LVC125; SO-14_3.9x8.65mm_P1.27mm
U3: MIC5504-3.3YM5; SOT-23-5

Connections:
+3V3: C1.1, C4.1, J1.2, R1.1, U1.8 (VCC), U2.14 (VCC), U3.5 (VOUT)
+5V: C3.1, J1.1, U3.1 (VIN), U3.3 (EN)
/CS_3V3: R1.2, U1.2 (CS_SD3), U2.3
/CS_VCC: J1.7, U2.1, U2.2, U2.4, U2.10, U2.13
/MISO_3V3: U1.6 (MISO_SD0), U2.9
/MISO_ILIM_SD: R2.1, U2.8
/MISO_VCC: J1.5, R2.2
/MOSI_3V3: U1.5 (CMD_MOSI), U2.11
/MOSI_VCC: J1.6, U2.12
/SCK_3V3: U1.3 (SCK), U2.6
/SCK_VCC: J1.4, U2.5
GND: C1.2, C3.2, C4.2, J1.3, U1.4 (GND), U2.7 (GND), U3.2 (GND)

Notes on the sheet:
SOURCE
5V0 3V3 GND SCK MISO MOSI CS
BYPASS SHARED WITH C1

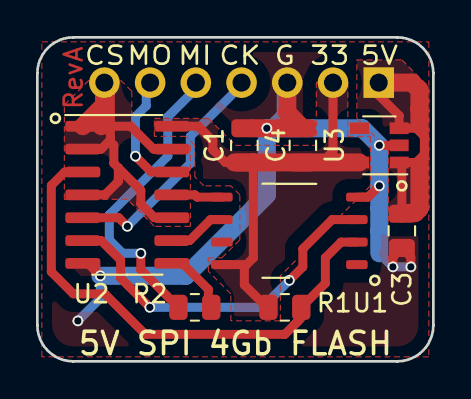
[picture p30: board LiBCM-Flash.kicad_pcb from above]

Board: 4 copper layers, 22.0 x 18.0 mm, 9 parts (1 on the bottom side), 12 nets.

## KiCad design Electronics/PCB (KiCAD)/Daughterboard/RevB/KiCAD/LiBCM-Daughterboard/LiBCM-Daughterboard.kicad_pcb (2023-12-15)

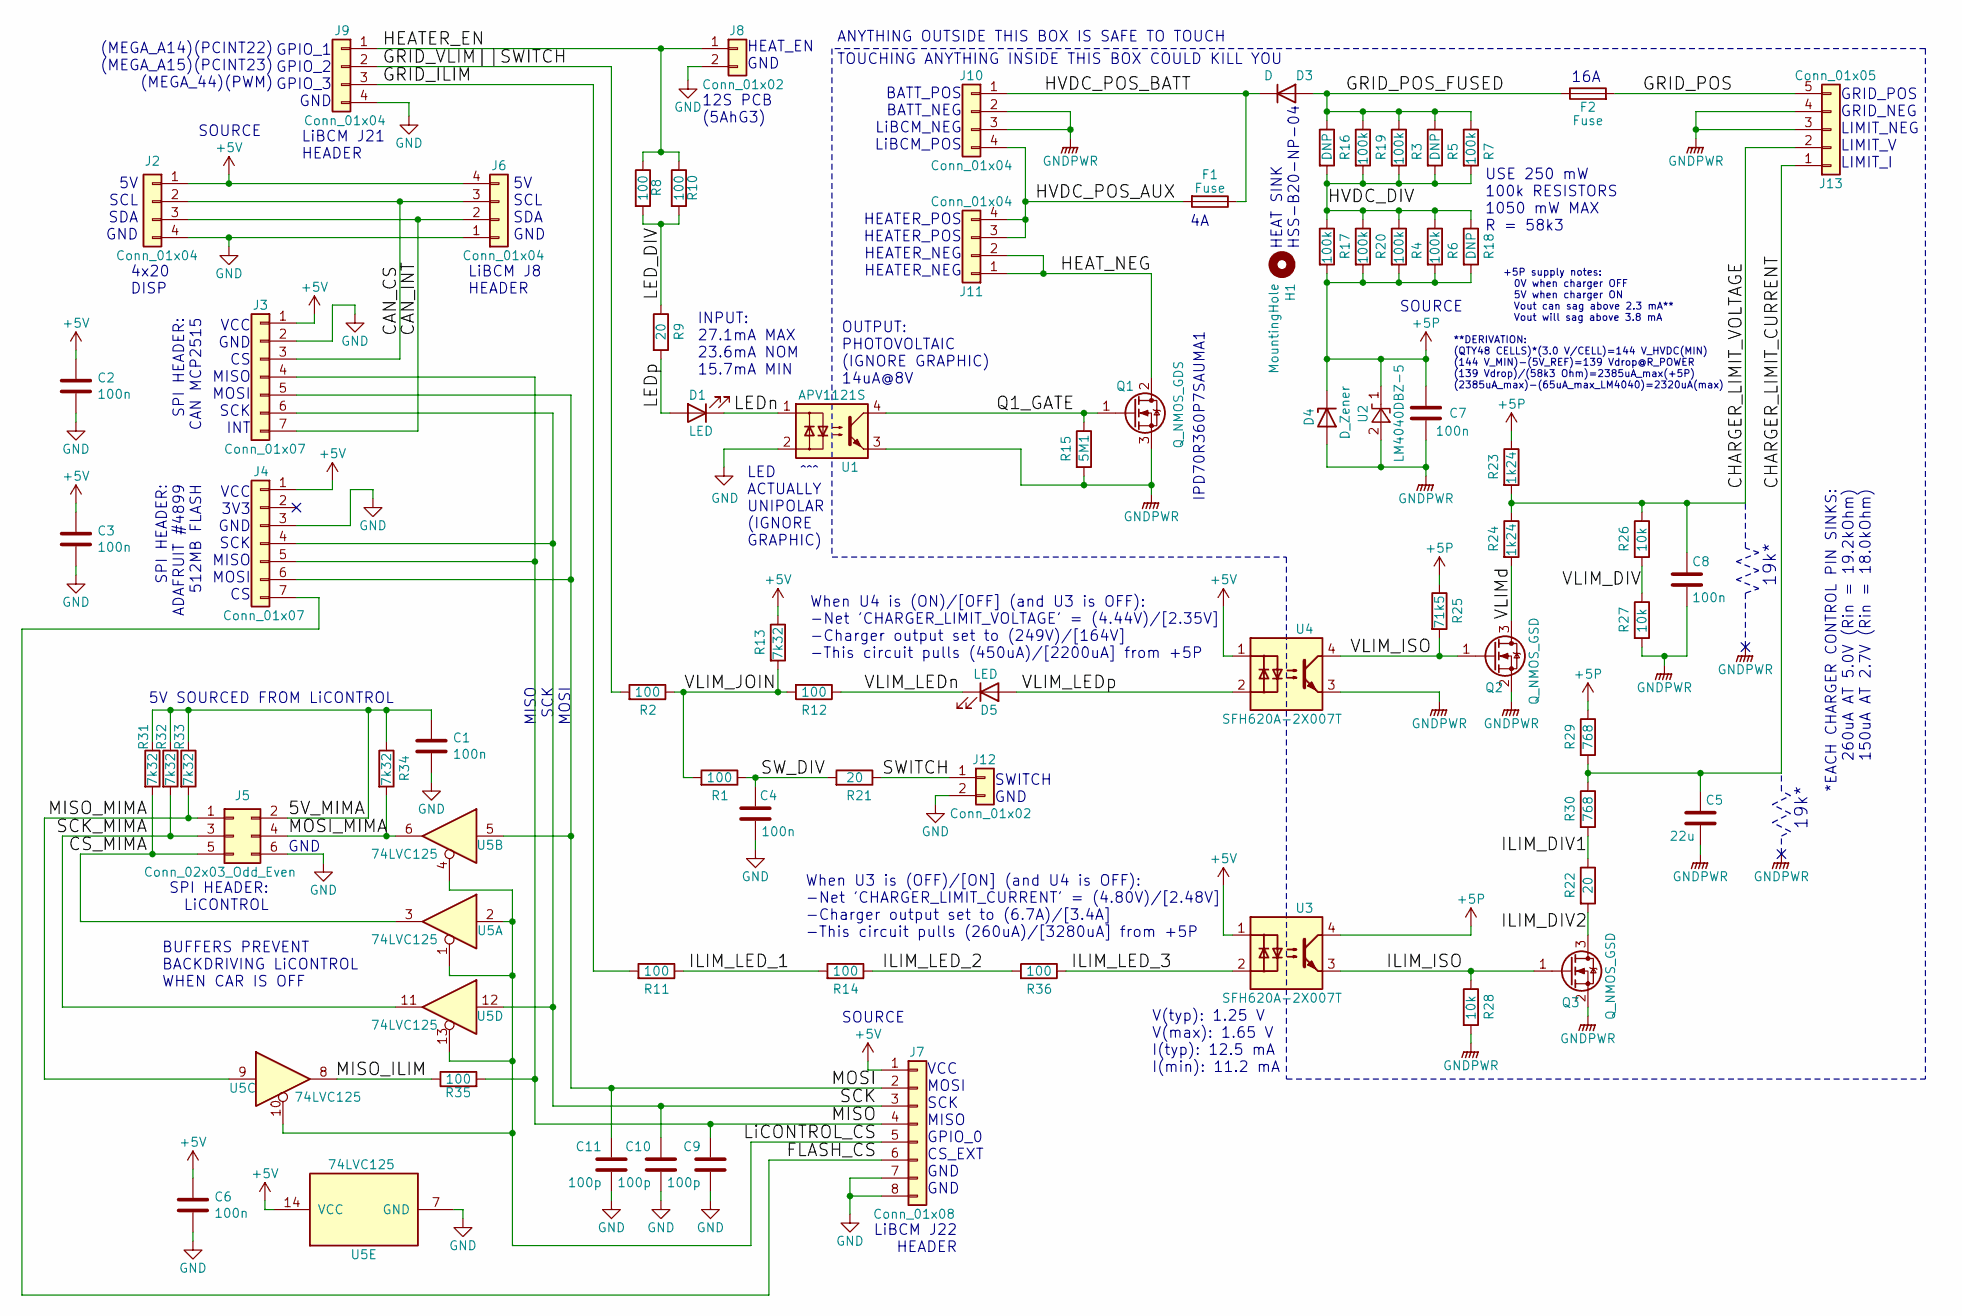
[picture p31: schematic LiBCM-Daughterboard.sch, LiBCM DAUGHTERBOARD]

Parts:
C1, C2, C3, C4, C6, C7, C8: 100n; C_0805_2012Metric
C5: 22u; C_1210_3225Metric
C9, C10, C11: 100p; C_0805_2012Metric
D1, D5: LED; LED_0805_2012Metric
D3: D; TO-220-2_Horizontal_TabDown
D4: D_Zener; D_SOD-123
F1, F2: Fuse; Fuseholder_Cylinder-5x20mm_Schurter_0031_8201_Horizontal_Op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
H1: MountingHole; MountingHole_3.2mm_M3
J2, J6, J9: Conn_01x04; PinHeader_1x04_P2.54mm_Vertical
J3, J4: Conn_01x07; PinHeader_1x07_P2.54mm_Vertical
J5: Conn_02x03_Odd_Even; PinHeader_2x03_P2.54mm_Vertical
J7: Conn_01x08; PinHeader_1x08_P2.54mm_Vertical
J8, J12: Conn_01x02; PinHeader_1x02_P2.54mm_Vertical
J10, J11: Conn_01x04; PhoenixContact_MCV_1,5_4-G-3.5_1x04_P3.50mm_Vertical
J13: Conn_01x05; PhoenixContact_MCV_1,5_5-G-3.5_1x05_P3.50mm_Vertical
Q1: Q_NMOS_GDS; TO-252-3_TabPin2
Q2, Q3: Q_NMOS_GSD; SOT-23
R1, R2, R8, R10, R11, R12, R14, R35, R36: 100; R_0805_2012Metric
R3, R4, R6, R7, R17, R19, R20: 100k; R_0805_2012Metric
R5, R16, R18: DNP; R_0805_2012Metric
R9, R21, R22: 20; R_0805_2012Metric
R13, R31, R32, R33, R34: 7k32; R_0805_2012Metric
R15: 5M1; R_1206_3216Metric
R23, R24: 1k24; R_0805_2012Metric
R25: 71k5; R_0805_2012Metric
R26, R27, R28: 10k; R_0805_2012Metric
R29, R30: 768; R_0805_2012Metric
U1: APV1121S; SOP-4_3.8x4.1mm_P2.54mm
U2: LM4040DBZ-5; SOT-23
U3, U4: SFH620A-2X007T; SMDIP-4_W9.53mm_Clearance8mm
U5: 74LVC125; SO-14_3.9x8.65mm_P1.27mm

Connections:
+5P: C7.1, D4.1 (K), R4.2, R6.2, R17.2, R18.2, R20.2, R23.1, R25.1, R29.1, U2.1 (K), U3.4
+5V: C2.1, C3.1, C6.1, J2.1, J3.1, J4.1, J6.4, J7.1, R13.1, U3.1, U4.1, U5.14 (VCC)
/5V_MIMA: C1.1, J5.2, R31.1, R32.1, R33.1, R34.1
/CAN_CS: J2.2, J3.3, J6.3
/CAN_INT: J2.3, J3.7, J6.2
/CHARGER_LIMIT_CURRENT: C5.1, J13.1, R29.2, R30.1
/CHARGER_LIMIT_VOLTAGE: C8.1, J13.2, R23.2, R24.1, R26.1
/CS_MIMA: J5.5, R31.2, U5.3
/FLASH_CS: J4.7, J7.6
/GRID_ILIM: J9.3, R11.2
/GRID_POS: F2.2, J13.5
/GRID_POS_FUSED: D3.2 (A), F2.1, R3.1, R5.1, R7.1, R16.1, R19.1
/GRID_VLIM||SWITCH: J9.2, R2.2
/HEATER_EN: J8.1, J9.1, R8.1, R10.1
/HEAT_NEG: J11.1, J11.2, Q1.2 (D)
/HVDC_DIV: R3.2, R4.1, R5.2, R6.1, R7.2, R16.2, R17.1, R18.1, R19.2, R20.1
/HVDC_POS_AUX: F1.2, J10.4, J11.3, J11.4
/HVDC_POS_BATT: D3.1 (K), F1.1, J10.1
/ILIM_DIV1: R22.1, R30.2
/ILIM_DIV2: Q3.3 (D), R22.2
/ILIM_ISO: Q3.1 (G), R28.1, U3.3
/ILIM_LED_1: R11.1, R14.2
/ILIM_LED_2: R14.1, R36.2
/ILIM_LED_3: R36.1, U3.2
/LED_DIV: R8.2, R9.1, R10.2
/LEDn: D1.1 (K), U1.1
/LEDp: D1.2 (A), R9.2
/LiCONTROL_CS: J7.5, U5.1, U5.2, U5.4, U5.10, U5.13
/MISO: C9.1, J3.4, J4.5, J7.4, R35.2
/MISO_ILIM: R35.1, U5.8
/MISO_MIMA: J5.1, R33.2, U5.9
/MOSI: C11.1, J3.5, J4.6, J7.2, U5.5
/MOSI_MIMA: J5.4, R34.2, U5.6
/Q1_GATE: Q1.1 (G), R15.1, U1.4
/SCK: C10.1, J3.6, J4.4, J7.3, U5.12
/SCK_MIMA: J5.3, R32.2, U5.11
/SWITCH: J12.1, R21.1
/SW_DIV: C4.1, R1.1, R21.2
/VLIM_DIV: R26.2, R27.1
/VLIM_ISO: Q2.1 (G), R25.2, U4.4
/VLIM_JOIN: R1.2, R2.1, R12.2, R13.2
/VLIM_LEDn: D5.1 (K), R12.1
/VLIM_LEDp: D5.2 (A), U4.2
/VLIMd: Q2.3 (D), R24.2
GND: C1.2, C2.2, C3.2, C4.2, C6.2, C9.2, C10.2, C11.2, J2.4, J3.2, J4.3, J5.6, J6.1, J7.7, J7.8, J8.2, J9.4, J12.2, U1.2, U5.7 (GND)
GNDPWR: C5.2, C7.2, C8.2, D4.2 (A), J10.2, J10.3, J13.3, J13.4, Q1.3 (S), Q2.2 (S), Q3.2 (S), R15.2, R27.2, R28.2, U1.3, U2.2 (A), U4.3

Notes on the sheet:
GPIO_1 GPIO_2 GPIO_3 GND
SPI HEADER: CAN MCP2515
OUTPUT: PHOTOVOLTAIC (IGNORE GRAPHIC) 14uA@8V
LED ^^^ ACTUALLY UNIPOLAR (IGNORE GRAPHIC)
IPD70R360P7SAUMA1
LiBCM J21 HEADER
HEATER_POS HEATER_POS HEATER_NEG HEATER_NEG
(MEGA_A14)(PCINT22) (MEGA_A15)(PCINT23) (MEGA_44)(PWM)
SPI HEADER: ADAFRUIT #4899 512MB FLASH
VCC 3V3 GND SCK MISO MOSI CS
VCC GND CS MISO MOSI SCK INT
LiBCM J22 HEADER
VCC MOSI SCK MISO GPIO_0 CS_EXT GND GND
16A
*EACH CHARGER CONTROL PIN SINKS: 260uA AT 5.0V (Rin = 19.2kOhm) 150uA AT 2.7V (Rin = 18.0kOhm)
GRID_POS GRID_NEG LIMIT_NEG LIMIT_V LIMIT_I
BATT_POS BATT_NEG LiBCM_NEG LiBCM_POS
TOUCHING ANYTHING INSIDE THIS BOX COULD KILL YOU
ANYTHING OUTSIDE THIS BOX IS SAFE TO TOUCH
INPUT: 27.1mA MAX 23.6mA NOM 15.7mA MIN
5V SCL SDA GND
LiBCM J8 HEADER
4x20 DISP
HEAT SINK HSS-B20-NP-04
SOURCE
V(typ): 1.25 V V(max): 1.65 V I(typ): 12.5 mA I(min): 11.2 mA
SPI HEADER: LiCONTROL
MISO SCK MOSI
12S PCB (5AhG3)
HEAT_EN GND
19k*
When U4 is (ON)/[OFF] (and U3 is OFF): -Net 'CHARGER_LIMIT_VOLTAGE' = (4.44V)/[2.35V] -Charger output set to (249V)/[164V] -This circuit pulls (450uA)/[2200uA] from +5P
SWITCH GND
When U3 is (OFF)/[ON] (and U4 is OFF): -Net 'CHARGER_LIMIT_CURRENT' = (4.80V)/[2.48V] -Charger output set to (6.7A)/[3.4A] -This circuit pulls (260uA)/[3280uA] from +5P
USE 250 mW 100k RESISTORS 1050 mW MAX R = 58k3
+5P supply notes: 0V when charger OFF 5V when charger ON Vout can sag above 2.3 mA** Vout will sag above 3.8 mA
**DERIVATION: (QTY48 CELLS)*(3.0 V/CELL)=144 V_HVDC(MIN) (144 V_MIN)-(5V_REF)=139 Vdrop@R_POWER (139 Vdrop)/(58k3 Ohm)=2385uA_max(+5P) (2385uA_max)-(65uA_max_LM4040)=2320uA(max)
GND
BUFFERS PREVENT BACKDRIVING LiCONTROL WHEN CAR IS OFF
5V SOURCED FROM LiCONTROL

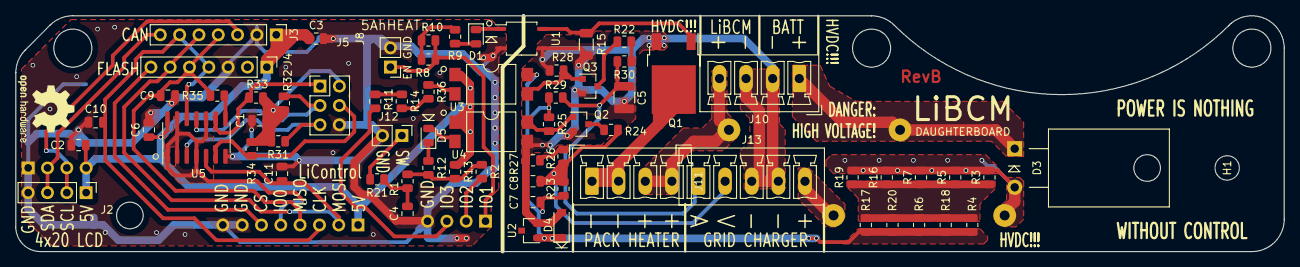
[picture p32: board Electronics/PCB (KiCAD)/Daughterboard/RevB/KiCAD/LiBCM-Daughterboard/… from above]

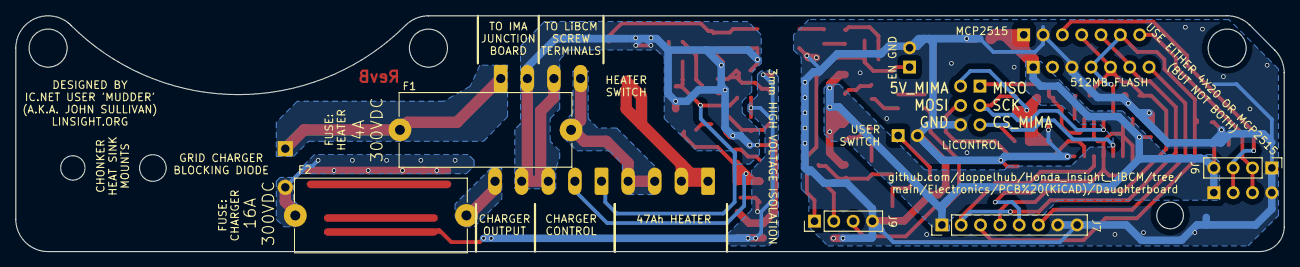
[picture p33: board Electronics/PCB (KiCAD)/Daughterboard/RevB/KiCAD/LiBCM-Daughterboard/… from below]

Board: 4 copper layers, 166.8 x 31.0 mm, 74 parts (5 on the bottom side), 46 nets.

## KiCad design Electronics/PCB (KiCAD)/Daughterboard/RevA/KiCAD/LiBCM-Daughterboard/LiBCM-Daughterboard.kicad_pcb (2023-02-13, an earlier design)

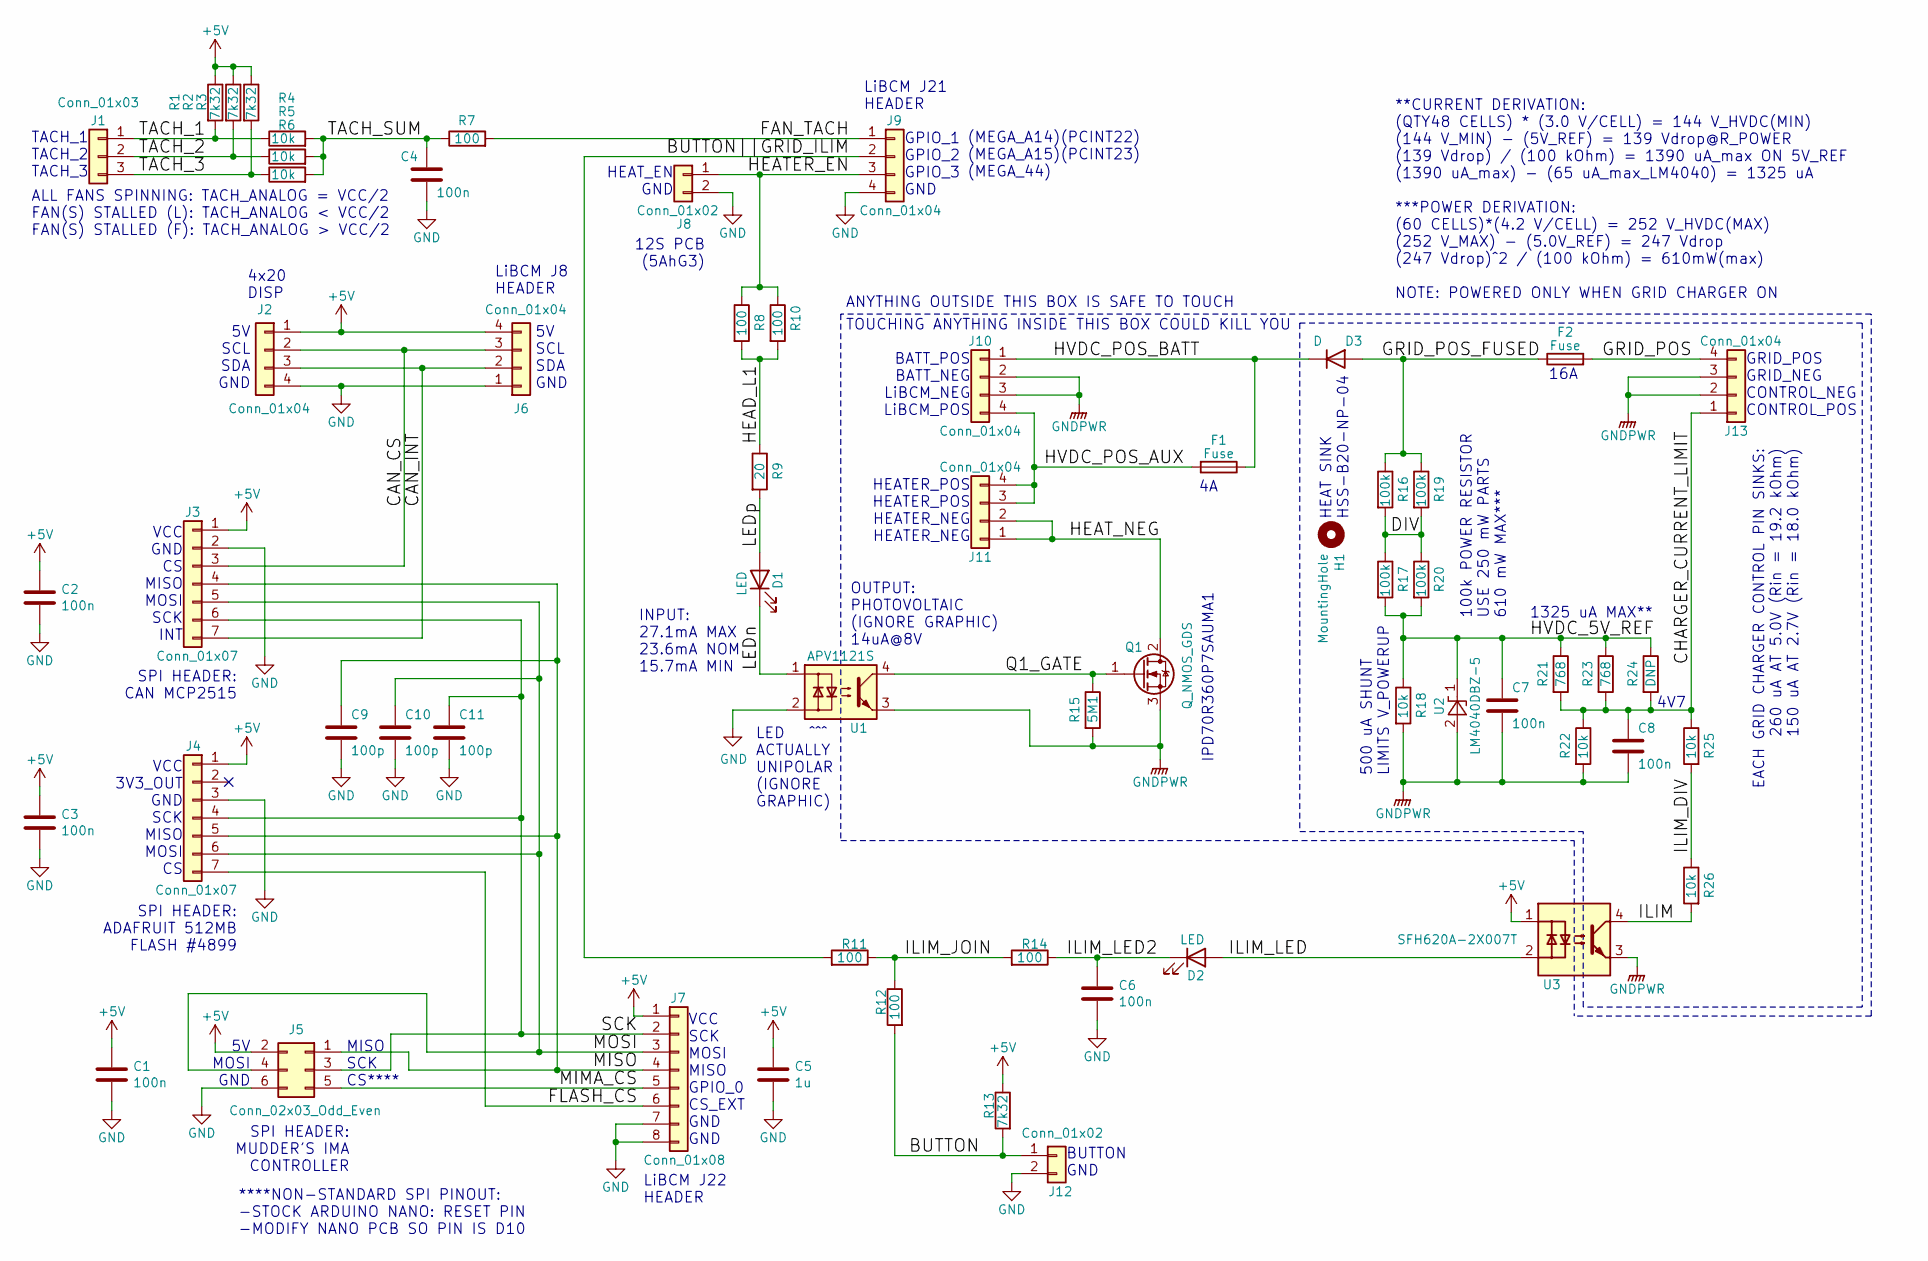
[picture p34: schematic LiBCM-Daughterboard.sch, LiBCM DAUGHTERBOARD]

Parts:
C1, C2, C3, C4, C6, C7, C8: 100n; C_0805_2012Metric
C5: 1u; C_0805_2012Metric
C9, C10, C11: 100p; C_0805_2012Metric
D1, D2: LED; LED_0805_2012Metric
D3: D; TO-220-2_Horizontal_TabDown
F1, F2: Fuse; Fuseholder_Cylinder-5x20mm_Schurter_0031_8201_Horizontal_Op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
H1: MountingHole; MountingHole_3.2mm_M3
J1: Conn_01x03; PhoenixContact_MCV_1,5_3-G-3.5_1x03_P3.50mm_Vertical
J2, J6, J9: Conn_01x04; PinHeader_1x04_P2.54mm_Vertical
J3, J4: Conn_01x07; PinHeader_1x07_P2.54mm_Vertical
J5: Conn_02x03_Odd_Even; PinHeader_2x03_P2.54mm_Vertical
J7: Conn_01x08; PinHeader_1x08_P2.54mm_Vertical
J8, J12: Conn_01x02; PinHeader_1x02_P2.54mm_Vertical
J10, J11, J13: Conn_01x04; PhoenixContact_MCV_1,5_4-G-3.5_1x04_P3.50mm_Vertical
Q1: Q_NMOS_GDS; TO-252-3_TabPin2
R1, R2, R3, R13: 7k32; R_0805_2012Metric
R4, R5, R6, R18, R22, R25, R26: 10k; R_0805_2012Metric
R7, R8, R10, R11, R12, R14: 100; R_0805_2012Metric
R9: 20; R_0805_2012Metric
R15: 5M1; R_1206_3216Metric
R16, R17, R19, R20: 100k; R_0805_2012Metric
R21, R23: 768; R_0805_2012Metric
R24: DNP; R_0805_2012Metric
U1: APV1121S; SOP-4_4.4x2.6mm_P1.27mm
U2: LM4040DBZ-5; SOT-23
U3: SFH620A-2X007T; SMDIP-4_W9.53mm_Clearance8mm

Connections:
+5V: C1.1, C2.1, C3.1, C5.1, J2.1, J3.1, J4.1, J5.2, J6.4, J7.1, R1.1, R2.1, R3.1, R13.1, U3.1
/BUTTON: J12.1, R12.2, R13.2
/BUTTON||GRID_ILIM: J9.2, R11.2
/CAN_CS: J2.2, J3.3, J6.3
/CAN_INT: J2.3, J3.7, J6.2
/CHARGER_CURRENT_LIMIT: C8.1, J13.1, R21.2, R22.1, R23.2, R24.2, R25.1
/DIV: R16.2, R17.1, R19.2, R20.1
/FAN_TACH: J9.1, R7.2
/FLASH_CS: J4.7, J7.6
/GRID_POS: F2.2, J13.4
/GRID_POS_FUSED: D3.2 (A), F2.1, R16.1, R19.1
/HEAD_L1: R8.2, R9.1, R10.2
/HEATER_EN: J8.1, J9.3, R8.1, R10.1
/HEAT_NEG: J11.1, J11.2, Q1.2 (D)
/HVDC_5V_REF: C7.1, R17.2, R18.1, R20.2, R21.1, R23.1, R24.1, U2.1 (K)
/HVDC_POS_AUX: F1.2, J10.4, J11.3, J11.4
/HVDC_POS_BATT: D3.1 (K), F1.1, J10.1
/ILIM: R26.2, U3.4
/ILIM_DIV: R25.2, R26.1
/ILIM_JOIN: R11.1, R12.1, R14.2
/ILIM_LED: D2.2 (A), U3.2
/ILIM_LED2: C6.1, D2.1 (K), R14.1
/LEDn: D1.1 (K), U1.1
/LEDp: D1.2 (A), R9.2
/MIMA_CS: J5.5, J7.5
/MISO: C9.1, J3.4, J4.5, J5.1, J7.4
/MOSI: C10.1, J3.5, J4.6, J5.4, J7.3
/Q1_GATE: Q1.1 (G), R15.1, U1.4
/SCK: C11.1, J3.6, J4.4, J5.3, J7.2
/TACH_1: J1.1, R1.2, R4.1
/TACH_2: J1.2, R2.2, R5.1
/TACH_3: J1.3, R3.2, R6.1
/TACH_SUM: C4.1, R4.2, R5.2, R6.2, R7.1
GND: C1.2, C2.2, C3.2, C4.2, C5.2, C6.2, C9.2, C10.2, C11.2, J2.4, J3.2, J4.3, J5.6, J6.1, J7.7, J7.8, J8.2, J9.4, J12.2, U1.2
GNDPWR: C7.2, C8.2, J10.2, J10.3, J13.2, J13.3, Q1.3 (S), R15.2, R18.2, R22.2, U1.3, U2.2 (A), U3.3

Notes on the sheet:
GPIO_1 GPIO_2 GPIO_3 GND
TACH_1 TACH_2 TACH_3
SPI HEADER: CAN MCP2515
OUTPUT: PHOTOVOLTAIC (IGNORE GRAPHIC) 14uA@8V
LED ^^^ ACTUALLY UNIPOLAR (IGNORE GRAPHIC)
IPD70R360P7SAUMA1
HEAT_EN GND
LiBCM J21 HEADER
SPI HEADER: MUDDER'S IMA CONTROLLER
HEATER_POS HEATER_POS HEATER_NEG HEATER_NEG
ALL FANS SPINNING: TACH_ANALOG = VCC/2 FAN(S) STALLED (L): TACH_ANALOG < VCC/2 FAN(S) STALLED (F): TACH_ANALOG > VCC/2
(MEGA_A14)(PCINT22) (MEGA_A15)(PCINT23) (MEGA_44)
SPI HEADER: ADAFRUIT 512MB FLASH #4899
VCC 3V3_OUT GND SCK MISO MOSI CS
VCC GND CS MISO MOSI SCK INT
LiBCM J22 HEADER
VCC SCK MOSI MISO GPIO_0 CS_EXT GND GND
12S PCB (5AhG3)
16A
EACH GRID CHARGER CONTROL PIN SINKS: 260 uA AT 5.0V (Rin = 19.2 kOhm) 150 uA AT 2.7V (Rin = 18.0 kOhm)
1325 uA MAX**
100k POWER RESISTOR USE 250 mW PARTS 610 mW MAX***
**CURRENT DERIVATION: (QTY48 CELLS) * (3.0 V/CELL) = 144 V_HVDC(MIN) (144 V_MIN) - (5V_REF) = 139 Vdrop@R_POWER (139 Vdrop) / (100 kOhm) = 1390 uA_max ON 5V_REF (1390 uA_max) - (65 uA_max_LM4040) = 1325 uA ***POWER DERIVATION: (60 CELLS)*(4.2 V/CELL) = 252 V_HVDC(MAX) (252 V_MAX) - (5.0V_REF) = 247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
4V7
500 uA SHUNT LIMITS V_POWERUP
GRID_POS GRID_NEG CONTROL_NEG CONTROL_POS
BATT_POS BATT_NEG LiBCM_NEG LiBCM_POS
TOUCHING ANYTHING INSIDE THIS BOX COULD KILL YOU
ANYTHING OUTSIDE THIS BOX IS SAFE TO TOUCH
MISO SCK CS****
5V MOSI GND
****NON-STANDARD SPI PINOUT: -STOCK ARDUINO NANO: RESET PIN -MODIFY NANO PCB SO PIN IS D10
INPUT: 27.1mA MAX 23.6mA NOM 15.7mA MIN
BUTTON GND
5V SCL SDA GND
LiBCM J8 HEADER
4x20 DISP
HEAT SINK HSS-B20-NP-04

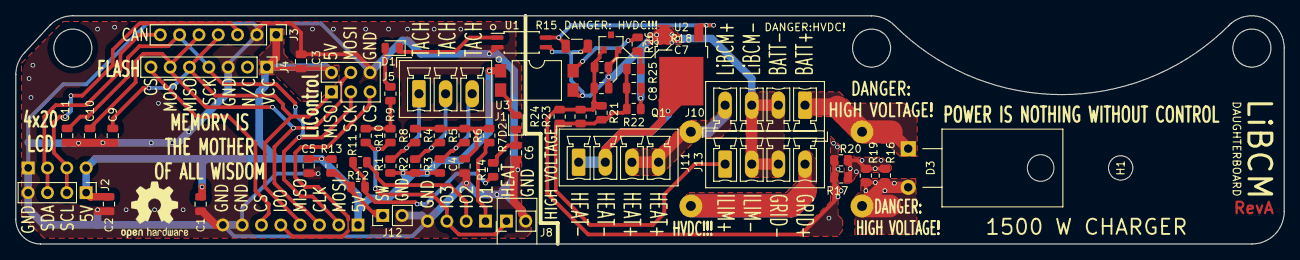
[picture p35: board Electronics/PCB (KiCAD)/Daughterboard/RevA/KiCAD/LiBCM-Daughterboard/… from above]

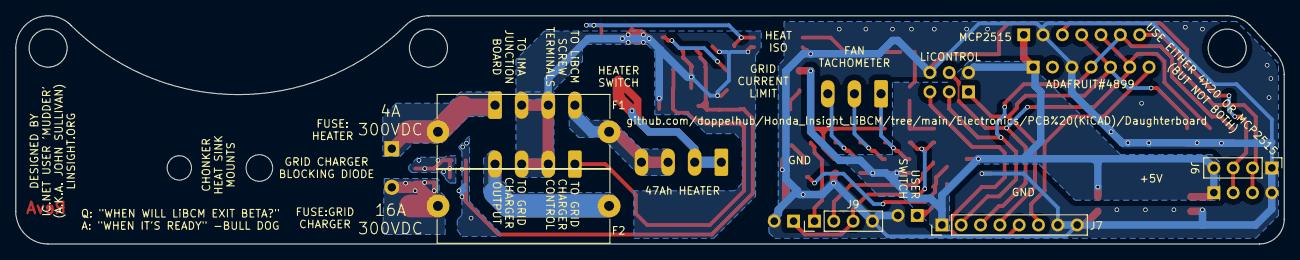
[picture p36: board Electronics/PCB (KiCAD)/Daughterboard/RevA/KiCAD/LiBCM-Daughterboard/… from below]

Board: 4 copper layers, 166.8 x 30.0 mm, 60 parts (5 on the bottom side), 35 nets.

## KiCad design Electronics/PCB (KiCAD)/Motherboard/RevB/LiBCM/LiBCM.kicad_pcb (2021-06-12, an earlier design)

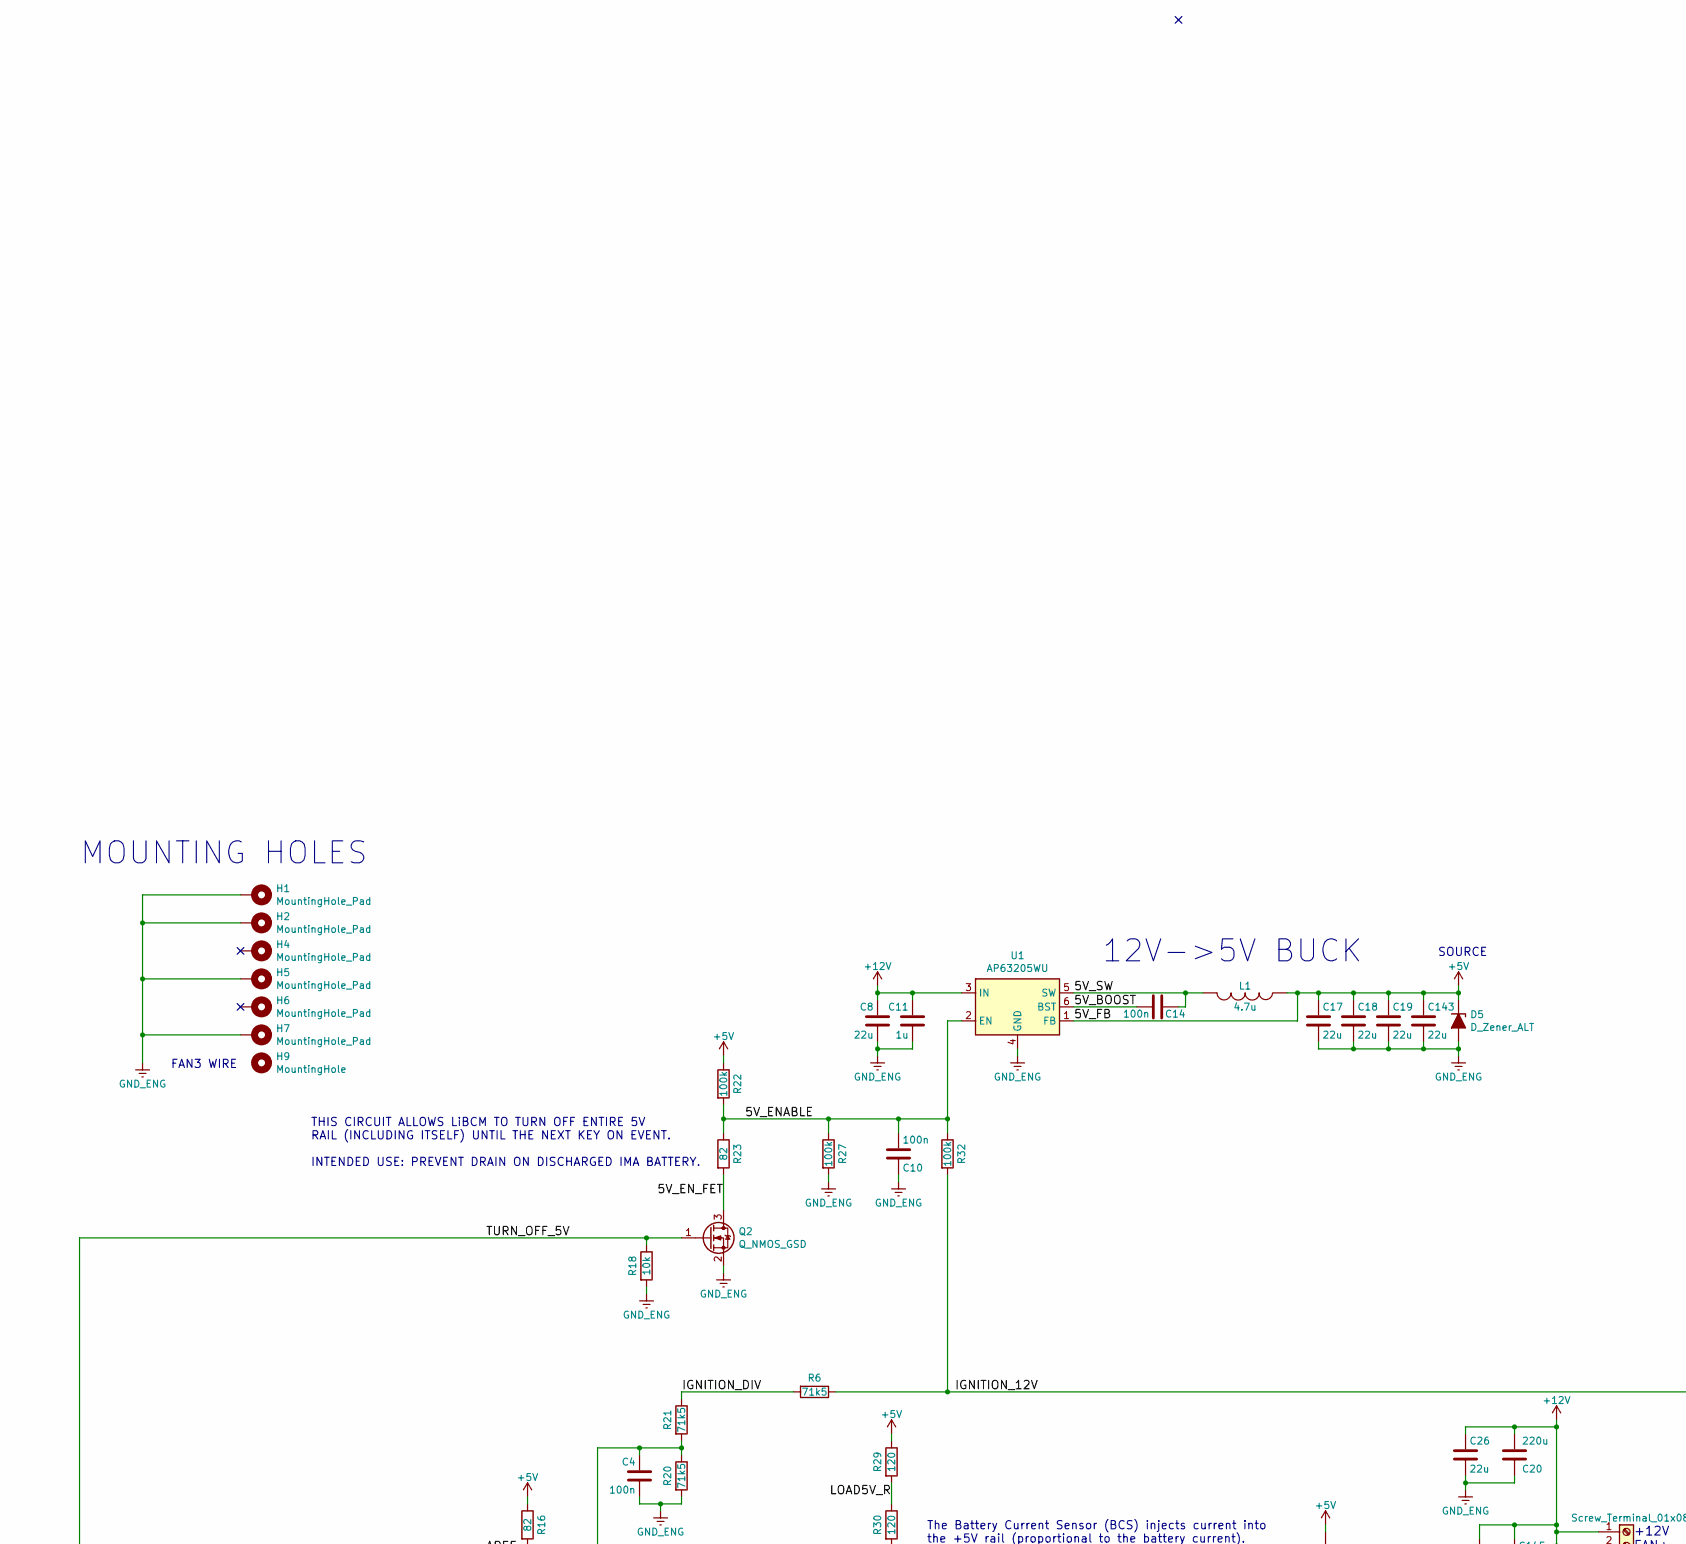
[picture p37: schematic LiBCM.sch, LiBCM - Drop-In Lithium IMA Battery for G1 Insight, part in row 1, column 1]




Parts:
C1, C2, C11, C13, C21, C24, C144, C147: 1u; C_0805_2012Metric
C3: 10n; C_0805_2012Metric
C4, C5, C6, C7, C9, C10, C12, C14, C15, C16, C22, C29, C149: 100n; C_0805_2012Metric
C8, C17, C18, C19, C23, C25, C26, C143, C145, C146: 22u; C_1210_3225Metric
C20, C27, C28: 220u; CP_Elec_10x10
C30: 33u; CP_Radial_D22.0mm_P10.00mm_SnapIn
C31, C152: 68n; C_1206_3216Metric
C32, C153, C154: DNP; C_1206_3216Metric
C33, C148, C150, C151: 22n; C_1206_3216Metric
C156: DNP; C_0805_2012Metric
D1, D2, D3, D4, D14, D15, D16: LED; LED_0805_2012Metric_Castellated
D5: D_Zener_ALT; D_SOD-123
D6: Q_TRIAC_A1A2G; TO-252-3_TabPin2
D11, D12, D13: 1N4148W; D_SOD-123
F1, F2: Fuse; Fuseholder_Cylinder-5x20mm_Schurter_0031_8201_Horizontal_Op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
H1, H2, H4, H5, H6, H7: MountingHole_Pad; MountingHole_6mm_Pad
H9: MountingHole; MountingHole_3mm
J1, J2, J3, J5, J6, J7: Conn_01x08; PinHeader_1x08_P2.54mm_Vertical
J4: Conn_02x03_Odd_Even; PinHeader_2x03_P2.54mm_Vertical
J8: Screw_Terminal_01x06; PinHeader_1x06_P2.54mm_Vertical
J9, J11: Screw_Terminal_01x08; CONN_1751303
J10: Screw_Terminal_01x03; SolderWire-1sqmm_1x03_P5.4mm_D1.4mm_OD2.7mm
J14: Conn_01x04; PinHeader_1x04_P2.54mm_Vertical
J15: Conn_01x02; PinHeader_1x02_P2.54mm_Vertical
L1: 4.7u; L_TDK_SLF7045
L2, L3: 1u; L_0805_2012Metric
M1, M2, M3: Fan; FAN_60x60OD_50x50Holes
P1: OEM_BCM_Connector; CONN_BCM_174917-6
P2: Conn_WallPlug_Earth; SolderWire-1sqmm_1x03_P5.4mm_D1.4mm_OD2.7mm
Q1, Q2, Q3, Q4, Q5, Q6, Q7, Q74, Q76: Q_NMOS_GSD; SOT-23
Q75: Q_PMOS_GSD; SOT-23; Digikey BSS308PE-H6327TR-ND
R1, R2, R3, R5, R43, R44, R45, R46, R58: 1k; R_0805_2012Metric
R6, R20, R21, R66: 71k5; R_0805_2012Metric
R13, R18, R26, R34, R35, R36, R37, R38, R39, R42, R47, R49, R51, R52, R55, R56, R61, R312, R315, R319: 10k; R_0805_2012Metric
R16, R23, R50, R53, R316, R317: 82; R_0805_2012Metric
R17, R29, R30, R40, R41, R68, R311: 120; R_0805_2012Metric
R19, R48, R80, R313, R314: DNP; R_0805_2012Metric
R22, R27, R32, R67, R74, R75, R77, R79: 100k; R_0805_2012Metric
R24, R25, R28, R31, R33, R60, R320: 3k3; R_0805_2012Metric
R54, R59, R63, R65, R78: 220; R_0805_2012Metric
R57: 7k32; R_0805_2012Metric
R69, R72: 10k@0.25W; R_0805_2012Metric
R70, R71: 20k@0.5W; R_0805_2012Metric
R73: 75; R_2010_5025Metric
R76: DNP; R_2010_5025Metric
SW1: SW_Push; Panasonic_EVQPUJ_EVQPUA
SW2: SW_DIP_x02; SW_DIP_SPSTx02_Slide_9.78x7.26mm_W8.61mm_P2.54mm
U1: AP63205WU; TSOT-23-6
U2, U3: LT1487; SOIC-8_3.9x4.9mm_P1.27mm
U4: LT1797; TSOT-23-5
U5: MOC3023M; SMDIP-6_W9.53mm
U6, U7: SFH620A-2X007T; SMDIP-4_W9.53mm_Clearance8mm
U8: EPM1210SJ; DCDC-EPM1210SJ
U9: H11D1SR2VM; SMDIP-6_W9.53mm

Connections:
+5V: C1.1, C2.1, C15.1, C16.1, C17.1, C18.1, C19.1, C29.1, C143.1, D5.1 (K), J1.5, J8.3, J14.1, L1.1, R16.1, R22.1, R29.1, R35.1, R36.1, R37.1, R38.1, R43.1, R45.1, R54.2, R61.1, R311.2, R316.1, R317.1, SW1.2, SW2.3, U1.1 (FB), U2.8 (VCC), U3.8 (VCC), U4.5 (V+); also elsewhere on the board
+12V: C8.1, C11.1, C20.1, C26.1, C28.1, C145.1, C146.1, D13.1 (K), J9.1, J9.2, J9.3, J9.4, L2.2, Q75.2 (S), R313.1, R319.1, U1.3 (IN)
/5V_BOOST: C14.2, U1.6 (BST)
/5V_ENABLE: C10.2, R22.2, R23.1, R27.1, R32.1, U1.2 (EN)
/5V_EN_FET: Q2.3 (D), R23.2
/5V_SW: C14.1, L1.2, U1.5 (SW)
/12NEG_UNFILTERED: C23.2, C25.2, C27.2, C147.2, C148.2, C149.1, L3.2, U8.7 (DC_OUT-)
/12POS_UNFILTERED: C23.1, C25.1, C27.1, C147.1, C149.2, L2.1, U8.5 (DC_OUT+)
/12V_ALWAYS: D11.1 (K), D12.1 (K), P1.A13 (WHT/RED_VBU)
/AREF: C3.1, J5.8, R16.2
/BATTFANH: D12.2 (A), P1.A24 (BLU/YEL_BATTFANH), Q5.3 (D)
/BATTFANH_EN: J2.3, Q5.1 (G), R42.1
/BATTFANL: D11.2 (A), P1.A11 (BLU/BLK_BATTFANL), Q6.3 (D)
/BATTFANL_EN: J2.2, Q6.1 (G), R47.1
/BATTSCI1: P1.A20 (ORG/ORG_BATTSCI1), R41.2, R46.1, U3.6 (A)
/BATTSCI2: P1.A07 (WHT/WHT_BATTSCI2), R41.1, R45.2, U3.7 (B)
/BATTSCI_DE: J3.3, U3.3 (Drv_Out_En)
/BATTSCI_REn: J3.4, U3.2 (Rec_Out_En)
/BATTSCI_RX: J7.5, U3.1 (Rec_Out)
/BATTSCI_TX: J7.6, U3.4 (Drv_Inp)
/BATT_CURRENT_I2V: C22.1, R51.1, R52.2, U4.3 (IN+)
/BATT_CURRENT_SCALED: J2.1, R67.1, U4.1 (OUT)
/FAN-: C145.2, D13.2 (A), J9.5, J9.6, J9.7, Q7.3 (D)
/FAN_PWM: J5.4, R58.1
/FAN_PWM_G: C156.1, Q7.1 (G), R49.1, R58.2, SW1.1
/GPIO-1: J4.1, J8.4
/GRID_EN: D14.2 (A), J5.3
/GRID_EN_LED_A: D14.1 (K), U5.1
/GRID_EN_LED_C: R59.2, U5.2
/GRID_PWM: D15.2 (A), J5.1
/GRID_PWM+: J11.1, R80.1, U7.4
/GRID_PWM-: J11.2, R80.2, U7.3
/GRID_PWM_LED_A: D15.1 (K), U7.1
/GRID_PWM_LED_C: R63.2, U7.2
/GRID_SENSE: C24.1, J5.2, R60.2
/GRID_SENSE_L1: R74.2, R75.2, U6.1
/GRID_SENSE_L2: R77.2, R79.2, U6.2
/GRID_SENSE_NOISY: R60.1, R61.2, U6.4
/HLINE_CONN: P1.B01 ((HLINE)), R17.1
/HLINE_JUMPER: J15.2, R17.2
/HMI_EN: J3.2, Q1.1 (G), R13.1
/HMI_EN_OD: J14.4, Q1.3 (D)
/HMI_RX: J7.3, J14.2
/HMI_TX: J7.4, J14.3, J15.1
/HVDC_POS_UNFUSED: F2.1, J11.8
/IGNITION_12V: P1.A01 (PNK/BLU_IGA2), P1.A02 (PNK/BLU_IGA1), R6.1, R32.2, R313.2
/IGNITION_DIV: R6.2, R21.1
/IGNITION_SENSE: C4.1, J5.6, R19.2, R20.1, R21.2
/I_SENSOR_EN: J5.5, Q3.1 (G), Q74.1 (G), Q76.1 (G), R19.1, R26.1
/I_SENSOR_NEG: C21.2, P1.A16 (LTGRN/LTGRN_IPWR_N), Q76.3 (D)
/I_SENSOR_POS: C21.1, P1.A03 (BLU/RED_IPWR_P), Q75.3 (D)
/I_SENSOR_RAW: P1.A04 (RED/WHT_ISOC), R50.2, R51.2, R53.2
/L1: F1.2, P2.1 (AC_P)
/L1_FUSED: D6.2 (A2), F1.1, R73.1, R74.1, R75.1, R76.2
/L1_GRID: C32.1, C33.1, D6.1 (A1), J10.1, R78.1
/L2: J10.2, P2.2 (AC_N), R77.1, R79.1
/LED1: J3.5, R1.2
/LED1R: D1.2 (A), R1.1
/LED2: J3.6, R2.2
/LED2R: D2.2 (A), R2.1
/LED3: J3.7, R3.2
/LED3R: D3.2 (A), R3.1
/LED4: J3.8, R5.2
/LED4R: D4.2 (A), R5.1
/LOAD5V_FET: Q3.3 (D), R30.2
/LOAD5V_R: R29.2, R30.1
/MCM_E_B: R315.2, U9.6
/MCM_E_C: R70.1, R314.2, U9.5
/MCM_E_CONN+: C31.2, J11.5, R69.2, R70.2
/MCM_E_CONN-: C31.1, J11.6, R71.1, R72.1
/MCM_E_CONTROL: D16.2 (A), J6.8
/MCM_E_E: R71.2, R314.1, R315.1, U9.4
/MCM_E_LED_A: D16.1 (K), U9.1
/MCM_E_LED_C: R65.2, U9.2
/METSCI1: P1.A21 (WHT/BLU_METSCI1), R40.2, R44.1, U2.6 (A)
/METSCI2: P1.A08 (BLU/ORG_METSCI2), R40.1, R43.2, U2.7 (B)
/METSCI_DE: J6.3, U2.3 (Drv_Out_En)
/METSCI_REn: J6.4, U2.2 (Rec_Out_En)
/METSCI_RX: J7.7, U2.1 (Rec_Out)
/METSCI_TX: J7.8, U2.4 (Drv_Inp)
/NEG_SAFETY: C148.1, C150.2
/OP_GAIN: R55.1, R56.2, R66.2
/OP_IN-: R66.1, R67.2, U4.4 (IN-)
/OP_OFFSET_H: R54.1, R55.2
/OP_OFFSET_L: R56.1, R57.2
/Q74D: Q74.3 (D), R320.2
/Q75G: Q75.1 (G), R319.2, R320.1
/RESETcap: C144.1, R311.1, SW2.4
/RESETn: J1.3, SW2.1
/SCL: J7.1, J8.2
/SDA: J7.2, J8.1
/SENSE_MID: R50.1, R53.1, R316.2, R317.2
/SNUB: C32.2, R76.1
/SPI_BATT_CS0: J4.6; also elsewhere on the board
/SPI_BATT_MISO: J4.3, P1.B02 ((SPI_MISO)); also elsewhere on the board
/SPI_BATT_MOSI: J4.4, P1.B03 ((SPI_MOSI)); also elsewhere on the board
/SPI_BATT_SCK: J4.5, P1.B04 ((SPI_CLK)); also elsewhere on the board
/SPI_EXTERNAL_CS1: J6.6, P1.B05 ((SPI_CS1))
/TBATT_BLU: P1.B19 (BLU/BLU_TBATT4), R31.1, R38.2
/TBATT_BLU_LPF: C9.2, J2.7, R31.2
/TBATT_GRN: P1.B20 (GRN/GRN_TBATT2), R25.1, R36.2
/TBATT_GRN_LPF: C6.2, J2.5, R25.2
/TBATT_SG: P1.B12 (BLK/BLK_TBATT_SG), Q4.3 (D)
/TBATT_WHT: P1.B08 (WHT/WHT_TBATT3), R28.1, R37.2
/TBATT_WHT_LPF: C7.2, J2.6, R28.2
/TBATT_YEL: P1.B09 (YEL/YEL_TBATT1), R24.1, R35.2
/TBATT_YEL_LPF: C5.2, J2.4, R24.2
/TEMP_SENSOR_EN: J6.7, Q4.1 (G), R39.1
/TRIAC_DRIVE: R68.2, U5.6
/TRIAC_GATE: D6.3 (G), R78.2, U5.4
/TRIAC_SNUBBER: C33.2, R68.1, R73.2
/TURN_OFF_5V: J3.1, Q2.1 (G), R18.1
/USER_SW: J4.2, R312.1, SW2.2
/VPIN_IN: C12.1, J2.8, R33.2
/VPIN_IN_NOISY: P1.B11 (RED/RED_(VPIN_IN)), R33.1, R48.1
/VPIN_OUT_LPF: C13.1, P1.B22 (BLK/BLK_(VPIN_OUT)), R34.1, R48.2
/VPIN_OUT_PWM: J6.5, R34.2
GND_CHASSIS: J10.3, P1.A12 (BLK/BLK_PG1), P1.A25 (BLK/BLK_PG2), P2.3 (EARTH)
GND_ENG: C1.2, C2.2, C3.2, C4.2, C5.1, C6.1, C7.1, C8.2, C9.1, C10.1, C11.2, C12.2, C13.2, C15.2, C16.2, C17.2, C18.2, C19.2, C20.2, C22.2, C24.2, C26.2, C28.2, C29.2, C143.2, C144.2, C146.2, C156.2, D1.1 (K), D2.1 (K), D3.1 (K), D4.1 (K), D5.2 (A), H1.1, H2.1, H5.1, H7.1, J1.6, J1.7, J5.7, J8.5, J8.6, J9.8, L3.1, P1.A14 (BRN/YEL_LG2), P1.A15 (BRN/YEL_LG1), Q1.2 (S), Q2.2 (S), Q3.2 (S), Q4.2 (S), Q5.2 (S), Q6.2 (S), Q7.2 (S), Q74.2 (S), Q76.2 (S), R13.2, R18.2, R20.2, R26.2, R27.2, R39.2, R42.2, R44.2, R46.2, R47.2, R49.2, R52.1, R57.1, R59.1, R63.1, R65.1, R312.2, U1.4 (GND), U2.5 (GND), U3.5 (GND), U4.2 (V-), U6.3; also elsewhere on the board
HVDC_NEG: C30.2, C150.1, C151.1, C152.1, C153.1, C154.1, J11.3, J11.7, R72.2, U8.10 (HVDC_IN-)
HVDC_POS_FUSED: C30.1, C151.2, C152.2, C153.2, C154.2, F2.2, J11.4, R69.1, U8.12 (HVDC_IN+)

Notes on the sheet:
12V->5V BUCK
OEM BCM A+B CONNECTORS
MOUNTING HOLES
2021MAR24
John Sullivan - 2021 - IC.net: 'mudder' This work is licensed under the Creative Commons Attribution-ShareAlike 4.0 International License (CC BY-SA 4.0). View this license at: creativecommons.org/licenses/by-sa/4.0/
+12V FAN+ FAN+ FAN+ FAN- FAN- FAN- GND_ENG
MEGA_N/C MEGA_IOREF MEGA_RESET MEGA_3V3 MEGA_5V0 MEGA_GND MEGA_GND MEGA_Vin
MEGA_A0 MEGA_A1 MEGA_A2 MEGA_A3 MEGA_A4 MEGA_A5 MEGA_A6 MEGA_A7
MEGA_A8 MEGA_A9 MEGA_A10 MEGA_A11 MEGA_A12 MEGA_A13 MEGA_A14 MEGA_A15
MEGA_AREF MEGA_GND MEGA_13 MEGA_12 MEGA_11 MEGA_10 MEGA_9 MEGA_8
MEGA_7 MEGA_6 MEGA_5 MEGA_4 MEGA_3 MEGA_2 MEGA_1(TX0) MEGA_0(RX0)
MEGA_14(TX3) MEGA_15(RX3) MEGA_16(TX2) MEGA_17(RX2) MEGA_18(TX1) MEGA_19(RX1) MEGA_20(SDA) MEGA_21(SCL)
2.4 mA @ 240AC = 576 mW 1.2 mA @ 120AC = 144 mW
GRID_L1 GRID_L2(N) GRID_GND
GRID CHARGER HLG-320H-C1400B MUST BE "B" VERSION
GRID_PWM+ GRID_PWM- GRID_HVDC- GRID_HVDC+ MCM_CONN_E+ MCM_CONN_E- JUNCTION_HVDC- JUNCTION_HVDC+
MCM
IMA BATTERY
GALVANIC ISOLATION
M_53(SS)
USED TO TELL WHEN CAR IS ON. LiBCM GENERATES +12V FROM IMA BATTERY.
+12V <- HVDC
The Battery Current Sensor (BCS) injects current into the +5V rail (proportional to the battery current). If the sum of all loads on the +5V rail is less than the current injected by the BCS, then the single-quadrant 12V->5V DCDC converter will fall out of regulation, thus causing the voltage on +5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
R_I2V: 82 OHMS
V_MIN = 1.75 V_MAX = 4.00 SENSOR RAILS AT THESE VALUES
Battery Current Sensor outputs 250 uA/A (ISOC). The output voltage is ratiometric to +5V rail. Therefore ADC should reference +5V rail. BATT_CURRENT_I2V is 2.5 volts with no battery current. ASSIST causes OUTPUT voltage to increase. REGEN causes OUTPUT voltage to decrease. The voltage measured on B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
BATT_CURRENT_SCALED
V_MIN = 0.05 V_MAX = 4.95
Applies: m= 2.29 gain b= -4.07 offset
The output voltage is ratiometric to +5V rail. Therefore ADC should reference +5V rail. BATT_CURRENT_SCALED is 1.660 volts with no battery current. ASSIST causes OUTPUT voltage to increase. REGEN causes OUTPUT voltage to decrease. The voltage measured on BATT_CURRENT_SCALED is: (BATT_CURRENT_I2V) *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
TOUCHING ANYTHING IN THIS BOX COULD KILL YOU
ANYTHING OUTSIDE THE BOX IS SAFE TO TOUCH
THIS CIRCUIT ALLOWS LiBCM TO TURN OFF ENTIRE 5V RAIL (INCLUDING ITSELF) UNTIL THE NEXT KEY ON EVENT. INTENDED USE: PREVENT DRAIN ON DISCHARGED IMA BATTERY.
GRID_EN
GRID_SENSE
GRID_PWM
SPI_EXTERNAL_CS1
SPI_BATT_SCK
SPI_BATT_MOSI
SPI_BATT_MISO

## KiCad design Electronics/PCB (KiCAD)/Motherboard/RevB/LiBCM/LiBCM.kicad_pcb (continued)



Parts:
C34, C49, C50, C70, C73, C94, C97, C117, C118, C135, C136: 100n; C_0805_2012Metric
C35, C36, C37, C38, C39, C40, C41, C42, C43, C44, C45, C46, C47, C57, C58, C59, C60, C61, C62, C63, C64, C65, C66, C67, C68, C69, C79, C80, C81, C82, C83, C84, C85, C86, C87, C88, C89, C90, C91, C104, C105, C106, C107, C108, C109, C110, C111, C112, C113, C114, C115, C116, C122, C123, C124, C125, C126, C127, C128, C129, C130, C131, C132, C133, C134: 10n; C_0805_2012Metric
C48, C52, C77, C93, C103, C142: 20p; C_0805_2012Metric
C51, C53, C54, C74, C75, C76, C98, C99, C100, C119, C120, C121, C137, C138, C139: 1u; C_0805_2012Metric
C55, C56, C71, C72, C78, C92, C95, C96, C101, C102, C140, C141, C155: 22n; C_1206_3216Metric
D7, D8, D9, D10, D17: LED; LED_0805_2012Metric_Castellated
J12: Conn_01x02_Male; SolderWire-0.25sqmm_1x02_P4.2mm_D0.65mm_OD1.7mm
J13, J16: Conn_01x20; PinHeader_2x10_P2.54mm_Vertical
J17, J18: Conn_01x14; PinHeader_2x07_P2.54mm_Vertical
Q8, Q9, Q10, Q11, Q12, Q13, Q14, Q15, Q16, Q17, Q18, Q19, Q21, Q22, Q23, Q24, Q25, Q26, Q27, Q28, Q29, Q30, Q31, Q32, Q34, Q35, Q36, Q37, Q38, Q39, Q40, Q41, Q42, Q43, Q44, Q45, Q47, Q48, Q49, Q50, Q51, Q52, Q53, Q54, Q55, Q56, Q57, Q58, Q60, Q61, Q62, Q63, Q64, Q65, Q66, Q67, Q68, Q69, Q70, Q71: Q_PMOS_GSD; SOT-23; Digikey BSS308PE-H6327TR-ND
Q20, Q33, Q46, Q59, Q72: Q_NPN_BCEC; SOT-223; Digikey BCP56-16T1GOSTR-ND
R7, R8, R9, R10, R11, R81, R125, R128, R171, R174, R218, R221, R264, R267, R305, R308: 3k3; R_0805_2012Metric
R62, R64, R83, R84, R85, R86, R87, R88, R89, R90, R91, R92, R93, R94, R132, R133, R134, R135, R136, R137, R138, R139, R140, R141, R142, R143, R177, R178, R179, R180, R181, R182, R183, R184, R185, R186, R187, R188, R225, R226, R227, R228, R229, R230, R231, R232, R233, R234, R235, R236, R268, R269, R270, R271, R272, R273, R274, R275, R276, R277: 75; R_2010_5025Metric
R82, R130: 100k; R_0805_2012Metric
R95, R96, R97, R98, R99, R100, R101, R102, R103, R104, R105, R106, R107, R123, R124, R144, R145, R146, R147, R148, R149, R150, R151, R152, R153, R154, R155, R156, R169, R170, R189, R190, R191, R192, R193, R194, R195, R196, R197, R198, R199, R200, R201, R216, R217, R237, R238, R239, R240, R241, R242, R243, R244, R245, R246, R247, R248, R249, R262, R263, R278, R279, R280, R281, R282, R283, R284, R285, R286, R287, R288, R289, R290, R303, R304: 82; R_0805_2012Metric
R108, R109, R110, R111, R112, R113, R114, R115, R116, R117, R118, R119, R157, R158, R159, R160, R161, R162, R163, R164, R165, R166, R167, R168, R202, R203, R204, R205, R206, R207, R208, R209, R210, R211, R212, R213, R250, R251, R252, R253, R254, R255, R256, R257, R258, R259, R260, R261, R291, R292, R293, R294, R295, R296, R297, R298, R299, R300, R301, R302: 3.3k; R_0805_2012Metric
R120, R122, R126, R172, R219, R265, R306: 1k; R_0805_2012Metric
R121, R223: 120; R_0805_2012Metric
R127, R173, R220, R266, R307: 10k; R_0805_2012Metric
R129, R131, R175, R176, R214, R215, R222, R224, R309, R310: 5M; R_1206_3216Metric
T1, T3: Trans_7490100111; Trans_7490100111A
T2: Trans_7490100111; Trans_7490100111A; Digikey 7490100111A
TH1, TH2, TH3, TH4, TH5: THERMISTOR; R_0805_2012Metric
U10: LTC6820; LTC6820_MSOP
U11, U12, U13, U14, U15: LTC6804-2

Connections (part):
+5V: C34.1, R81.1, R82.1, U10.6 (VDDS), U10.7 (POL), U10.8 (PHA), U10.9 (VDD), U10.12 (MSTR); also elsewhere on the board
/LiBCM BMS/BIAS_A: R129.1, R131.2
/LiBCM BMS/BIAS_B: R175.2, R176.1
/LiBCM BMS/BIAS_C: R214.2, R215.1
/LiBCM BMS/BIAS_D: R222.2, R224.1
/LiBCM BMS/BIAS_E: R309.2, R310.1
/LiBCM BMS/C0_A: C41.2, C47.2, R107.1, U11.26 (C0)
/LiBCM BMS/C0_B: C63.2, C69.2, R156.1, U12.26 (C0)
/LiBCM BMS/C0_C: C85.2, C91.2, R201.1, U13.26 (C0)
/LiBCM BMS/C0_D: C110.2, C116.2, R249.1, U14.26 (C0)
/LiBCM BMS/C0_E: C128.2, C134.2, R290.1, U15.26 (C0)
/LiBCM BMS/C1_A: C40.2, C47.1, R106.1, U11.24 (C1)
/LiBCM BMS/C1_B: C62.2, C69.1, R155.1, U12.24 (C1)
/LiBCM BMS/C1_C: C84.2, C91.1, R200.1, U13.24 (C1)
/LiBCM BMS/C1_D: C109.2, C116.1, R248.1, U14.24 (C1)
/LiBCM BMS/C1_E: C127.2, C134.1, R289.1, U15.24 (C1)
/LiBCM BMS/C2_A: C40.1, C46.2, R105.1, U11.22 (C2)
/LiBCM BMS/C2_B: C62.1, C68.2, R154.1, U12.22 (C2)
/LiBCM BMS/C2_C: C84.1, C90.2, R199.1, U13.22 (C2)
/LiBCM BMS/C2_D: C109.1, C115.2, R247.1, U14.22 (C2)
/LiBCM BMS/C2_E: C127.1, C133.2, R288.1, U15.22 (C2)
/LiBCM BMS/C3_A: C39.2, C46.1, R104.1, U11.20 (C3)
/LiBCM BMS/C3_B: C61.2, C68.1, R153.1, U12.20 (C3)
/LiBCM BMS/C3_C: C83.2, C90.1, R198.1, U13.20 (C3)
/LiBCM BMS/C3_D: C108.2, C115.1, R246.1, U14.20 (C3)
/LiBCM BMS/C3_E: C126.2, C133.1, R287.1, U15.20 (C3)
/LiBCM BMS/C4_A: C39.1, C45.2, R103.1, U11.18 (C4)
/LiBCM BMS/C4_B: C61.1, C67.2, R152.1, U12.18 (C4)
/LiBCM BMS/C4_C: C83.1, C89.2, R197.1, U13.18 (C4)
/LiBCM BMS/C4_D: C108.1, C114.2, R245.1, U14.18 (C4)
/LiBCM BMS/C4_E: C126.1, C132.2, R286.1, U15.18 (C4)
/LiBCM BMS/C5_A: C38.2, C45.1, R102.1, U11.16 (C5)
/LiBCM BMS/C5_B: C60.2, C67.1, R151.1, U12.16 (C5)
/LiBCM BMS/C5_C: C82.2, C89.1, R196.1, U13.16 (C5)
/LiBCM BMS/C5_D: C107.2, C114.1, R244.1, U14.16 (C5)
/LiBCM BMS/C5_E: C125.2, C132.1, R285.1, U15.16 (C5)
/LiBCM BMS/C6_A: C38.1, C44.2, R101.1, U11.14 (C6)
/LiBCM BMS/C6_B: C60.1, C66.2, R150.1, U12.14 (C6)
/LiBCM BMS/C6_C: C82.1, C88.2, R195.1, U13.14 (C6)
/LiBCM BMS/C6_D: C107.1, C113.2, R243.1, U14.14 (C6)
/LiBCM BMS/C6_E: C125.1, C131.2, R284.1, U15.14 (C6)
/LiBCM BMS/C7_A: C37.2, C44.1, R100.1, U11.12 (C7)
/LiBCM BMS/C7_B: C59.2, C66.1, R149.1, U12.12 (C7)
/LiBCM BMS/C7_C: C81.2, C88.1, R194.1, U13.12 (C7)
/LiBCM BMS/C7_D: C106.2, C113.1, R242.1, U14.12 (C7)
/LiBCM BMS/C7_E: C124.2, C131.1, R283.1, U15.12 (C7)
/LiBCM BMS/C8_A: C37.1, C43.2, R99.1, U11.10 (C8)
/LiBCM BMS/C8_B: C59.1, C65.2, R148.1, U12.10 (C8)
/LiBCM BMS/C8_C: C81.1, C87.2, R193.1, U13.10 (C8)
/LiBCM BMS/C8_D: C106.1, C112.2, R241.1, U14.10 (C8)
/LiBCM BMS/C8_E: C124.1, C130.2, R282.1, U15.10 (C8)
/LiBCM BMS/C9_A: C36.2, C43.1, R98.1, U11.8 (C9)
/LiBCM BMS/C9_B: C58.2, C65.1, R147.1, U12.8 (C9)
/LiBCM BMS/C9_C: C80.2, C87.1, R192.1, U13.8 (C9)
/LiBCM BMS/C9_D: C105.2, C112.1, R240.1, U14.8 (C9)
/LiBCM BMS/C9_E: C123.2, C130.1, R281.1, U15.8 (C9)
/LiBCM BMS/C10_A: C36.1, C42.2, R97.1, U11.6 (C10)
/LiBCM BMS/C10_B: C58.1, C64.2, R146.1, U12.6 (C10)
/LiBCM BMS/C10_C: C80.1, C86.2, R191.1, U13.6 (C10)
/LiBCM BMS/C10_D: C105.1, C111.2, R239.1, U14.6 (C10)
/LiBCM BMS/C10_E: C123.1, C129.2, R280.1, U15.6 (C10)
/LiBCM BMS/C10pos: J13.11, Q10.2 (S), R84.2, R97.2
/LiBCM BMS/C11_A: C35.2, C42.1, R96.1, U11.4 (C11)
/LiBCM BMS/C11_B: C57.2, C64.1, R145.1, U12.4 (C11)
/LiBCM BMS/C11_C: C79.2, C86.1, R190.1, U13.4 (C11)
/LiBCM BMS/C11_D: C104.2, C111.1, R238.1, U14.4 (C11)
/LiBCM BMS/C11_E: C122.2, C129.1, R279.1, U15.4 (C11)
/LiBCM BMS/C11pos: J13.12, Q9.2 (S), R83.2, R96.2
/LiBCM BMS/C12_A: C35.1, R95.1, U11.2 (C12)
/LiBCM BMS/C12_B: C57.1, R144.1, U12.2 (C12)
/LiBCM BMS/C12_C: C79.1, R189.1, U13.2 (C12)
/LiBCM BMS/C12_D: C104.1, R237.1, U14.2 (C12)
/LiBCM BMS/C12_E: C122.1, R278.1, U15.2 (C12)
/LiBCM BMS/CELL1pos: J13.2, Q19.2 (S), R93.2, R106.2
/LiBCM BMS/CELL2pos: J13.3, Q18.2 (S), R92.2, R105.2
/LiBCM BMS/CELL3pos: J13.4, Q17.2 (S), R91.2, R104.2
/LiBCM BMS/CELL4pos: J13.5, Q16.2 (S), R90.2, R103.2
/LiBCM BMS/CELL5pos: J13.6, Q15.2 (S), R89.2, R102.2
/LiBCM BMS/CELL6pos: J13.7, Q14.2 (S), R88.2, R101.2
/LiBCM BMS/CELL7pos: J13.8, Q13.2 (S), R87.2, R100.2
/LiBCM BMS/CELL8pos: J13.9, Q12.2 (S), R86.2, R99.2
/LiBCM BMS/CELL9pos: J13.10, Q11.2 (S), R85.2, R98.2
/LiBCM BMS/CELL13pos: J13.14, Q32.2 (S), R142.2, R155.2
/LiBCM BMS/CELL14pos: J13.15, Q31.2 (S), R141.2, R154.2
/LiBCM BMS/CELL15pos: J13.16, Q30.2 (S), R140.2, R153.2
/LiBCM BMS/CELL16pos: J13.17, Q29.2 (S), R139.2, R152.2
/LiBCM BMS/CELL17pos: J13.18, Q28.2 (S), R138.2, R151.2
/LiBCM BMS/CELL18pos: J13.19, J16.1, Q27.2 (S), R137.2, R150.2
/LiBCM BMS/CELL19pos: J16.2, Q26.2 (S), R136.2, R149.2
/LiBCM BMS/CELL20pos: J16.3, Q25.2 (S), R135.2, R148.2
/LiBCM BMS/CELL21pos: J16.4, Q24.2 (S), R134.2, R147.2
/LiBCM BMS/CELL22pos: J16.5, Q23.2 (S), R133.2, R146.2
/LiBCM BMS/CELL23pos: J16.6, Q22.2 (S), R132.2, R145.2
/LiBCM BMS/CELL25pos: J16.8, Q45.2 (S), R187.2, R200.2
/LiBCM BMS/CELL26pos: J16.9, Q44.2 (S), R186.2, R199.2
/LiBCM BMS/CELL27pos: J16.10, Q43.2 (S), R185.2, R198.2
/LiBCM BMS/CELL28pos: J16.11, Q42.2 (S), R184.2, R197.2
/LiBCM BMS/CELL29pos: J16.12, Q41.2 (S), R183.2, R196.2
/LiBCM BMS/CELL30pos: J16.13, Q40.2 (S), R182.2, R195.2
/LiBCM BMS/CELL31pos: J16.14, Q39.2 (S), R181.2, R194.2
/LiBCM BMS/CELL32pos: J16.15, Q38.2 (S), R180.2, R193.2
/LiBCM BMS/CELL33pos: J16.16, Q37.2 (S), R179.2, R192.2
/LiBCM BMS/CELL34pos: J16.17, Q36.2 (S), R178.2, R191.2
/LiBCM BMS/CELL35pos: J16.18, Q35.2 (S), R177.2, R190.2
/LiBCM BMS/CELL36pos: J16.19, Q34.2 (S), R189.2, R216.1, R217.2
/LiBCM BMS/CELL37pos: J17.2, Q58.2 (S), R235.2, R248.2
/LiBCM BMS/CELL38pos: J17.3, Q57.2 (S), R234.2, R247.2
/LiBCM BMS/CELL39pos: J17.4, Q56.2 (S), R233.2, R246.2
/LiBCM BMS/CELL40pos: J17.5, Q55.2 (S), R232.2, R245.2
/LiBCM BMS/CELL41pos: J17.6, Q54.2 (S), R231.2, R244.2
/LiBCM BMS/CELL42pos: J17.7, Q53.2 (S), R230.2, R243.2
/LiBCM BMS/CELL43pos: J17.8, Q52.2 (S), R229.2, R242.2
/LiBCM BMS/CELL44pos: J17.9, Q51.2 (S), R228.2, R241.2
/LiBCM BMS/CELL45pos: J17.10, Q50.2 (S), R227.2, R240.2
/LiBCM BMS/CELL46pos: J17.11, Q49.2 (S), R226.2, R239.2
/LiBCM BMS/CELL47pos: J17.12, Q48.2 (S), R225.2, R238.2
/LiBCM BMS/CELL48pos: J17.13, Q47.2 (S), R237.2, R262.1, R263.2
/LiBCM BMS/CELL49pos: J18.2, Q71.2 (S), R276.2, R289.2
/LiBCM BMS/CELL50pos: J18.3, Q70.2 (S), R275.2, R288.2
/LiBCM BMS/CELL51pos: J18.4, Q69.2 (S), R274.2, R287.2
/LiBCM BMS/CELL52pos: J18.5, Q68.2 (S), R273.2, R286.2
/LiBCM BMS/CELL53pos: J18.6, Q67.2 (S), R272.2, R285.2
/LiBCM BMS/CELL54pos: J18.7, Q66.2 (S), R271.2, R284.2
/LiBCM BMS/CELL55pos: J18.8, Q65.2 (S), R270.2, R283.2
/LiBCM BMS/CELL56pos: J18.9, Q64.2 (S), R269.2, R282.2
/LiBCM BMS/CELL57pos: J18.10, Q63.2 (S), R268.2, R281.2
/LiBCM BMS/CELL58pos: J18.11, Q62.2 (S), R64.2, R280.2
/LiBCM BMS/CELL59pos: J18.12, Q61.2 (S), R62.2, R279.2
/LiBCM BMS/CELL60pos: J18.13, Q60.2 (S), R278.2, R303.1, R304.2
/LiBCM BMS/DRIVE_A: Q20.1 (B), U11.38 (DRIVE)
/LiBCM BMS/DRIVE_B: Q33.1 (B), U12.38 (DRIVE)
/LiBCM BMS/DRIVE_C: Q46.1 (B), U13.38 (DRIVE)
/LiBCM BMS/DRIVE_D: Q59.1 (B), U14.38 (DRIVE)
/LiBCM BMS/DRIVE_E: Q72.1 (B), U15.38 (DRIVE)
/LiBCM BMS/IB_6820: R120.1, U10.16 (IBIAS)
/LiBCM BMS/IB_A: R126.1, U11.44 (SDO(IBIAS))
/LiBCM BMS/IB_B: R172.1, U12.44 (SDO(IBIAS))
/LiBCM BMS/IB_C: R219.1, U13.44 (SDO(IBIAS))
/LiBCM BMS/IB_D: R265.1, U14.44 (SDO(IBIAS))
/LiBCM BMS/IB_E: R306.1, U15.44 (SDO(IBIAS))
/LiBCM BMS/IC_6820: R120.2, R122.1, U10.15 (ICMP)
/LiBCM BMS/IC_A: R7.2, R126.2, R128.2, U11.43 (SDI(ICMP))
/LiBCM BMS/IC_B: R8.2, R172.2, R174.2, U12.43 (SDI(ICMP))
/LiBCM BMS/IC_C: R9.2, R219.2, R221.2, U13.43 (SDI(ICMP))
/LiBCM BMS/IC_D: R10.2, R265.2, R267.2, U14.43 (SDI(ICMP))
/LiBCM BMS/IC_E: R11.2, R306.2, R308.2, U15.43 (SDI(ICMP))
/LiBCM BMS/IMA_A: T2.14, U11.41 (CSB(IMA))
/LiBCM BMS/IMA_B: T2.9, U12.41 (CSB(IMA))
/LiBCM BMS/IMA_C: T3.14, U13.41 (CSB(IMA))
/LiBCM BMS/IMA_D: T1.14, U14.41 (CSB(IMA))
/LiBCM BMS/IMA_E: T3.9, U15.41 (CSB(IMA))
/LiBCM BMS/IM_6820: R121.2, T1.9, U10.10 (IM)
/LiBCM BMS/IM_ISO_A: C55.2, T2.3
/LiBCM BMS/IM_ISO_B: C72.2, T2.8
/LiBCM BMS/IM_ISO_C: C92.2, T3.3
/LiBCM BMS/IM_ISO_D: C96.2, T1.3
/LiBCM BMS/IM_ISO_E: C141.2, T3.8
/LiBCM BMS/IM_ISO_EXT: C102.2, J12.1
/LiBCM BMS/IM_ISO_SAFETY: C55.1, C72.1, C92.1, C96.1, C102.1, C141.1, R223.1, T1.8
/LiBCM BMS/IPA_A: T2.16, U11.42 (SCK(IPA))
/LiBCM BMS/IPA_B: T2.11, U12.42 (SCK(IPA))
/LiBCM BMS/IPA_C: T3.16, U13.42 (SCK(IPA))
/LiBCM BMS/IPA_D: T1.16, U14.42 (SCK(IPA))
/LiBCM BMS/IPA_E: T3.11, U15.42 (SCK(IPA))
/LiBCM BMS/IP_6820: R121.1, T1.11, U10.11 (IP)
/LiBCM BMS/IP_ISO_A: C56.2, T2.1
/LiBCM BMS/IP_ISO_B: C71.2, T2.6
/LiBCM BMS/IP_ISO_C: C78.2, T3.1
/LiBCM BMS/IP_ISO_D: C95.2, T1.1
/LiBCM BMS/IP_ISO_E: C140.2, T3.6
/LiBCM BMS/IP_ISO_EXT: C101.2, J12.2
/LiBCM BMS/IP_ISO_SAFETY: C56.1, C71.1, C78.1, C95.1, C101.1, C140.1, R223.2, T1.6
/LiBCM BMS/ISO_TAP_A: R131.1, T2.2
/LiBCM BMS/ISO_TAP_B: R175.1, T2.7
/LiBCM BMS/ISO_TAP_C: R214.1, T3.2
/LiBCM BMS/ISO_TAP_D: R222.1, T1.2
/LiBCM BMS/ISO_TAP_E: R309.1, T3.7
/LiBCM BMS/LED_A: D7.2 (A), R125.1
/LiBCM BMS/LED_B: D8.2 (A), R171.1
/LiBCM BMS/LED_C: D9.2 (A), R218.1
/LiBCM BMS/LED_D: D10.2 (A), R264.1
/LiBCM BMS/LED_E: D17.2 (A), R305.1
/LiBCM BMS/QC1_A: Q19.3 (D), R94.1
/LiBCM BMS/QC1_B: Q32.3 (D), R143.1
/LiBCM BMS/QC1_C: Q45.3 (D), R188.1
/LiBCM BMS/QC1_D: Q58.3 (D), R236.1
/LiBCM BMS/QC1_E: Q71.3 (D), R277.1
/LiBCM BMS/QC2_A: Q18.3 (D), R93.1
/LiBCM BMS/QC2_B: Q31.3 (D), R142.1
/LiBCM BMS/QC2_C: Q44.3 (D), R187.1
/LiBCM BMS/QC2_D: Q57.3 (D), R235.1
/LiBCM BMS/QC2_E: Q70.3 (D), R276.1
/LiBCM BMS/QC3_A: Q17.3 (D), R92.1
/LiBCM BMS/QC3_B: Q30.3 (D), R141.1
/LiBCM BMS/QC3_C: Q43.3 (D), R186.1
/LiBCM BMS/QC3_D: Q56.3 (D), R234.1
/LiBCM BMS/QC3_E: Q69.3 (D), R275.1
/LiBCM BMS/QC4_A: Q16.3 (D), R91.1
/LiBCM BMS/QC4_B: Q29.3 (D), R140.1
/LiBCM BMS/QC4_C: Q42.3 (D), R185.1
/LiBCM BMS/QC4_D: Q55.3 (D), R233.1
/LiBCM BMS/QC4_E: Q68.3 (D), R274.1
/LiBCM BMS/QC5_A: Q15.3 (D), R90.1
/LiBCM BMS/QC5_B: Q28.3 (D), R139.1
/LiBCM BMS/QC5_C: Q41.3 (D), R184.1
/LiBCM BMS/QC5_D: Q54.3 (D), R232.1
/LiBCM BMS/QC5_E: Q67.3 (D), R273.1
/LiBCM BMS/QC6_A: Q14.3 (D), R89.1
/LiBCM BMS/QC6_B: Q27.3 (D), R138.1
/LiBCM BMS/QC6_C: Q40.3 (D), R183.1
/LiBCM BMS/QC6_D: Q53.3 (D), R231.1
/LiBCM BMS/QC6_E: Q66.3 (D), R272.1
/LiBCM BMS/QC7_A: Q13.3 (D), R88.1
/LiBCM BMS/QC7_B: Q26.3 (D), R137.1
/LiBCM BMS/QC7_C: Q39.3 (D), R182.1
/LiBCM BMS/QC7_D: Q52.3 (D), R230.1
/LiBCM BMS/QC7_E: Q65.3 (D), R271.1
/LiBCM BMS/QC8_A: Q12.3 (D), R87.1
/LiBCM BMS/QC8_B: Q25.3 (D), R136.1
/LiBCM BMS/QC8_C: Q38.3 (D), R181.1
/LiBCM BMS/QC8_D: Q51.3 (D), R229.1
/LiBCM BMS/QC8_E: Q64.3 (D), R270.1
/LiBCM BMS/QC9_A: Q11.3 (D), R86.1
/LiBCM BMS/QC9_B: Q24.3 (D), R135.1
/LiBCM BMS/QC9_C: Q37.3 (D), R180.1
/LiBCM BMS/QC9_D: Q50.3 (D), R228.1
/LiBCM BMS/QC9_E: Q63.3 (D), R269.1
/LiBCM BMS/QC10_A: Q10.3 (D), R85.1
/LiBCM BMS/QC10_B: Q23.3 (D), R134.1
/LiBCM BMS/QC10_C: Q36.3 (D), R179.1
/LiBCM BMS/QC10_D: Q49.3 (D), R227.1
/LiBCM BMS/QC10_E: Q62.3 (D), R268.1
/LiBCM BMS/QC11_A: Q9.3 (D), R84.1
/LiBCM BMS/QC11_B: Q22.3 (D), R133.1
/LiBCM BMS/QC11_C: Q35.3 (D), R178.1
/LiBCM BMS/QC11_D: Q48.3 (D), R226.1
/LiBCM BMS/QC11_E: Q61.3 (D), R64.1
/LiBCM BMS/QC12_A: Q8.3 (D), R83.1
/LiBCM BMS/QC12_B: Q21.3 (D), R132.1
/LiBCM BMS/QC12_C: Q34.3 (D), R177.1
/LiBCM BMS/QC12_D: Q47.3 (D), R225.1
/LiBCM BMS/QC12_E: Q60.3 (D), R62.1
/LiBCM BMS/S1_A: R119.1, U11.25 (S1)
/LiBCM BMS/S1_B: R168.1, U12.25 (S1)
/LiBCM BMS/S1_C: R213.1, U13.25 (S1)
/LiBCM BMS/S1_D: R261.1, U14.25 (S1)
/LiBCM BMS/S1_E: R302.1, U15.25 (S1)
/LiBCM BMS/S1b_A: Q19.1 (G), R119.2
/LiBCM BMS/S1b_B: Q32.1 (G), R168.2
/LiBCM BMS/S1b_C: Q45.1 (G), R213.2
/LiBCM BMS/S1b_D: Q58.1 (G), R261.2
/LiBCM BMS/S1b_E: Q71.1 (G), R302.2
/LiBCM BMS/S2_A: R118.1, U11.23 (S2)
/LiBCM BMS/S2_B: R167.1, U12.23 (S2)
/LiBCM BMS/S2_C: R212.1, U13.23 (S2)
/LiBCM BMS/S2_D: R260.1, U14.23 (S2)
/LiBCM BMS/S2_E: R301.1, U15.23 (S2)
/LiBCM BMS/S2b_A: Q18.1 (G), R118.2
/LiBCM BMS/S2b_B: Q31.1 (G), R167.2
/LiBCM BMS/S2b_C: Q44.1 (G), R212.2
/LiBCM BMS/S2b_D: Q57.1 (G), R260.2
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

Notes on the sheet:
0x2
0x3
C18+ C17+ C16+ C15+ C14+ C13+ C12+ C11+ C10+ C09+ C08+ C07+ C06+ C05+ C04+ C03+ C02+ C01+ C01-
(OPTIONAL) LT DC1942C Cells 61-72 0x7
0x5
Cell48+ Cell47+ Cell46+ Cell45+ Cell44+ Cell43+ Cell42+ Cell41+ Cell40+ Cell39+ Cell38+ Cell37+ Cell37-
Cell36+ Cell35+ Cell34+ Cell33+ Cell32+ Cell31+ Cell30+ Cell29+ Cell28+ Cell27+ Cell26+ Cell25+ Cell25-(24+) Cell23+ Cell22+ Cell21+ Cell20+ Cell19+ Cell19-(18+)
0x4
John Sullivan - 2021 - IC.net: 'mudder' This work is licensed under the Creative Commons Attribution-ShareAlike 4.0 International License (CC BY-SA 4.0). View this license at: creativecommons.org/licenses/by-sa/4.0/
LOAD RESISTORS (ERJ-12ZYJ750U): (4.1 V) ^ 2 / (75 Ohm) = (224 mW) per resistor. (4.1 V) / (75 Ohm) = (55 mA)
TOUCHING ANYTHING INSIDE THIS BOX IS SAFE
TOUCHING ANYTHING OUTSIDE THIS BOX COULD KILL YOU
GALVANIC ISOLATION
BATTERY BAY 1: 12S MODULE (CLOSEST TO JUNCTION BOARD) ALL 12 CELLS
BATTERY BAY 2: 18S MODULE (MIDDLE BAY) HIGHEST 12 CELLS
42S: LOWEST 6 CELLS BATTERY BAY 2 48S: LOWEST 6 CELLS BATTERY BAY 2 HIGHEST 6 CELLS BATTERY BAY 3
BATTERY BAY 3: 12S OR 18S LOWEST 12 CELLS
FOR 42S CONFIGURATION: -LEAVE PINS C13+ TO C18+ DISCONNECTED
U11/U12/U13 ARE NOT GALVANICALLY ISOLATED FROM EACH OTHER (BUT U14 IS)
U14 IS GALVANICALLY ISOLATED FROM U11/U12/U13. PLACE IMA FUSE+SWITCH BETWEEN BAY1 MODULE- AND BAY2 MODULE+
(SEE PAGE 1)
0x6
Cell60+ Cell59+ Cell58+ Cell57+ Cell56+ Cell55+ Cell54+ Cell53+ Cell52+ Cell51+ Cell50+ Cell49+ Cell49-
AUX BATTERY: 12S (NOT IN OEM ENCLOSURE)
U15 IS GALVANICALLY ISOLATED FROM ALL OTHERS. IF USED, PLACE BETWEEN PACK PACK POS & JUNC POS
isoSPI_EXT_P isoSPI_EXT_M
C12+ C11+ C10+ C09+ C08+ C07+ C06+ C05+ C04+ C03+ C02+ C01+ C01-
42S
48S

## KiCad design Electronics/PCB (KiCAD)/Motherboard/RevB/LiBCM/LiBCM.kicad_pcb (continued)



Board: 4 copper layers, 355.0 x 160.0 mm, 623 parts (6 on the bottom side), 529 nets.

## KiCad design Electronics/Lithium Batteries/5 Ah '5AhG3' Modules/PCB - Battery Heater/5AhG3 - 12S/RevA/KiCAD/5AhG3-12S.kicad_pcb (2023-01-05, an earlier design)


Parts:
D1: LED; LED_0805_2012Metric
F1: Fuse; Fuseholder_Cylinder-5x20mm_Schurter_0031_8201_Horizontal_Op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
J1: Screw_Terminal_01x02; PinHeader_1x02_P2.54mm_Vertical
J2: Screw_Terminal_01x02; PhoenixContact_MCV_1,5_2-G-3.5_1x02_P3.50mm_Vertical
J3, J4: Screw_Terminal_01x03; PhoenixContact_MCV_1,5_3-G-3.5_1x03_P3.50mm_Vertical
Q1: Q_NMOS_GDS; TO-252-3_TabPin2
R1, R2, R3, R4, R5, R6, R7, R8, R9, R10, R11, R12, R13, R14, R15, R16, R17, R18, R19, R20, R21, R22, R23, R24, R25, R26, R27, R28, R29, R30, R31, R32, R33, R34, R35, R36, R37, R38, R39, R40, R41, R42, R43, R44, R45, R46, R47, R48, R49, R50, R51, R52, R53, R54, R55, R56, R57, R58, R59, R60, R61, R62, R63, R64, R65, R66, R67, R68, R69, R70, R71, R72, R73, R74, R75, R76, R77, R78, R79, R80, R81, R82, R83, R84, R85, R86, R87, R88, R89, R90, R91, R92, R93, R94, R95, R96, R97, R98, R99, R100, R101, R102, R103, R104, R105, R106, R107, R108: 2k2; R_2010_5025Metric
R109, R110: 100; R_0805_2012Metric
R111: 5M1; R_1206_3216Metric
R112: 20; R_0805_2012Metric
U1: APV1121S; SOP-4_3.8x4.1mm_P2.54mm

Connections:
/GND_SAFE: J1.1, U1.2
/GPIO: J1.2, R109.1, R110.1
/GPIO_L1: R109.2, R110.2, R112.1
/HVDC_NEG: J2.1, Q1.3 (S), R111.2, U1.3
/HVDC_NEG_SWITCHED: J4.1, J4.2, J4.3, Q1.2 (D), R9.2, R18.2, R27.2, R36.2, R45.2, R54.2, R63.2, R72.2, R81.2, R90.2, R99.2, R108.2
/HVDC_POS: F1.1, J3.1, J3.2, J3.3, R1.1, R10.1, R19.1, R28.1, R37.1, R46.1, R55.1, R64.1, R73.1, R82.1, R91.1, R100.1
/HVDC_POS_UNFUSED: F1.2, J2.2
/LEDn: D1.1 (K), U1.1
/LEDp: D1.2 (A), R112.2
/Q1_GATE: Q1.1 (G), R111.1, U1.4
unnamed: R1.2, R2.1
unnamed: R2.2, R3.1
unnamed: R3.2, R4.1
unnamed: R4.2, R5.1
unnamed: R5.2, R6.1
unnamed: R6.2, R7.1
unnamed: R7.2, R8.1
unnamed: R8.2, R9.1
unnamed: R10.2, R11.1
unnamed: R11.2, R12.1
unnamed: R12.2, R13.1
unnamed: R13.2, R14.1
unnamed: R14.2, R15.1
unnamed: R15.2, R16.1
unnamed: R16.2, R17.1
unnamed: R17.2, R18.1
unnamed: R19.2, R20.1
unnamed: R20.2, R21.1
unnamed: R21.2, R22.1
unnamed: R22.2, R23.1
unnamed: R23.2, R24.1
unnamed: R24.2, R25.1
unnamed: R25.2, R26.1
unnamed: R26.2, R27.1
unnamed: R28.2, R29.1
unnamed: R29.2, R30.1
unnamed: R30.2, R31.1
unnamed: R31.2, R32.1
unnamed: R32.2, R33.1
unnamed: R33.2, R34.1
unnamed: R34.2, R35.1
unnamed: R35.2, R36.1
unnamed: R37.2, R38.1
unnamed: R38.2, R39.1
unnamed: R39.2, R40.1
unnamed: R40.2, R41.1
unnamed: R41.2, R42.1
unnamed: R42.2, R43.1
unnamed: R43.2, R44.1
unnamed: R44.2, R45.1
unnamed: R46.2, R47.1
unnamed: R47.2, R48.1
unnamed: R48.2, R49.1
unnamed: R49.2, R50.1
unnamed: R50.2, R51.1
unnamed: R51.2, R52.1
unnamed: R52.2, R53.1
unnamed: R53.2, R54.1
unnamed: R55.2, R56.1
unnamed: R56.2, R57.1
unnamed: R57.2, R58.1
unnamed: R58.2, R59.1
unnamed: R59.2, R60.1
unnamed: R60.2, R61.1
unnamed: R61.2, R62.1
unnamed: R62.2, R63.1
unnamed: R64.2, R65.1
unnamed: R65.2, R66.1
unnamed: R66.2, R67.1
unnamed: R67.2, R68.1
unnamed: R68.2, R69.1
unnamed: R69.2, R70.1
unnamed: R70.2, R71.1
unnamed: R71.2, R72.1
unnamed: R73.2, R74.1
unnamed: R74.2, R75.1
unnamed: R75.2, R76.1
unnamed: R76.2, R77.1
unnamed: R77.2, R78.1
unnamed: R78.2, R79.1
unnamed: R79.2, R80.1
unnamed: R80.2, R81.1
unnamed: R82.2, R83.1
unnamed: R83.2, R84.1
unnamed: R84.2, R85.1
unnamed: R85.2, R86.1
unnamed: R86.2, R87.1
unnamed: R87.2, R88.1
unnamed: R88.2, R89.1
unnamed: R89.2, R90.1
unnamed: R91.2, R92.1
unnamed: R92.2, R93.1
unnamed: R93.2, R94.1
unnamed: R94.2, R95.1
unnamed: R95.2, R96.1
unnamed: R96.2, R97.1
unnamed: R97.2, R98.1
unnamed: R98.2, R99.1
unnamed: R100.2, R101.1
unnamed: R101.2, R102.1
unnamed: R102.2, R103.1
unnamed: R103.2, R104.1
unnamed: R104.2, R105.1
unnamed: R105.2, R106.1
unnamed: R106.2, R107.1
unnamed: R107.2, R108.1

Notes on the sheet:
INPUT: 27.1mA MAX 23.6mA NOM 15.7mA MIN
GPIO GND
OUTPUT: PHOTOVOLTAIC (IGNORE GRAPHIC) 14uA@8V
V_GPIO = 0V: FET Q1 OFF V_GPIO = 5V: FET Q1 ON
INTERNAL LED ^^^ ACTUALLY UNIPOLAR (IGNORE GRAPHIC)
IPD70R360P7SAUMA1
HVDC+ HVDC-
TOUCHING ANYTHING OUTSIDE THIS BOX COULD KILL YOU
ANYTHING INSIDE THIS BOX IS SAFE TO TOUCH
HVDC+ HVDC+ HVDC+
HVDC_NEG_SWITCHED HVDC_NEG_SWITCHED HVDC_NEG_SWITCHED



Board: 2 copper layers, 240.5 x 124.0 mm, 120 parts (120 on the bottom side), 106 nets.

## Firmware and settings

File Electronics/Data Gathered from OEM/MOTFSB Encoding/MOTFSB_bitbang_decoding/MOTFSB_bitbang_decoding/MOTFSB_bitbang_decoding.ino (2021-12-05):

int MOTFSApin=12;
int MOTFSBpin=13;

//known good
//char frameorder[]={"bababababababababdbdbcbc"};

//test case: is babababa repeating acceptable input?
//char frameorder[]={"ba"};
//no CEL

//test case: add an 'E' frame
//char frameorder[]={"bababababababababebebcbc"};
//causes P1648 error (can't flash SCS codes because the MCM isn't connected).

//test case: add an 'E' frame in different spot
//char frameorder[]={"bababababababababdbdbebe"};
//same error (P1648).  Hence, error order doesn't appear to matter.

//can we broadcast just bdbdbcbc?
//char frameorder[]={"bdbdbcbc"};
//no CEL

//can we broadcast just bd?
//char frameorder[]={"bd"};
//no CEL

//can we broadcast just bc?
//char frameorder[]={"bc"};
//no CEL
//Thus, we can repeatedly broadcast any of the following without error: "bd" or "ba" or "bc"

//What if we repeatedly broadcast 'aaaaaaa'?
//char frameorder[]={"a"};
//P1645

//What about a made up sequence with previously good signals?
//char frameorder[]={"bababcbcbdbd"};
//no CEL

//What if we only broadcast each frame one time?
//char frameorder[]={"babcbd"};
//P1645... probably "data format" error.  Thus, we have to broadcast each packet twice

//What if we only broadcast an error every once in a while (note 'bebe' on the end)?
//char frameorder[]={"bababababababababababababababababababababababababababababababababebe"};
//Still get a P1648

//What if we wait longer between frames?
//char frameorder[]={"bba"};
//no CEL.  Thus, 'b' frame (all 0s) length isn't that important, as long as less than 5 seconds to send pattern twice.

//What if arbitrary # b-frames?:
//char frameorder[]={"babbabbbabbbba"};
//no CEL. Thus, 'b' frame (all 0s) length isn't that important, as long as less than 5 seconds to send pattern twice. 

//Let's make up a new frame 'g'=0b1111111100:
//char frameorder[]={"bababgbg"};
//no CEL

//Let's make up a new frame 'g'=0b1111111000:
//char frameorder[]={"bababgbg"};
//no CEL

//Let's make up a new frame 'g'=0b1111110000:
//char frameorder[]={"bababgbg"};
//no CEL

//Let's make up a new frame 'g'=0b1111100000:
//char frameorder[]={"bababgbg"};
//no CEL

//Let's make up a new frame 'g'=0b1111000000:
//char frameorder[]={"bababgbg"};
//no CEL

//Let's make up a new frame 'g'=0b1110000000:
//char frameorder[]={"bababgbg"};
//no CEL

//Let's make up a new frame 'g'=0b1100000000:
//char frameorder[]={"bababgbg"};
//no CEL

//Let's make up a new frame 'g'=0b1000000000:
//char frameorder[]={"bababgbg"};
//no CEL
//wonder if P codes are more than a single frame.  Earlier we got 3 P codes with just two 10 bit patterns ('E' & 'F').
//I suspect the ECU has a mask and is only looking for predefined IMA codes.

//Let's only use our new frame 'g'=0b1000000000:
//char frameorder[]={"bg"};
//no CEL

//What if we only broadcast '0' all the time? (24Hz clk still going):
//char frameorder[]={"b"};
//P1645

//Let's make up a new frame 'g'=0b1011001100 (loosely based on 'E'):
//char frameorder[]={"bg"};
//no CEL

//Let's make up a new frame 'g'=0b1111001100 (loosely based on 'E'):
//char frameorder[]={"bg"};
//P1577

//Let's make up a new frame 'g'=0b1011001000 (loosely based on above P1577):
//char frameorder[]={"bg"};
//no CEL

//Let's make up a new frame 'g'=0b1111000100 (loosely based on above P1577):
//char frameorder[]={"bg"};
//no CEL

//Let's make up a new frame 'g'=0b1110001100 (loosely based on above P1577):
//char frameorder[]={"bg"};
//P1439

//Let's make up a new frame 'g'=0b1100001100 (loosely based on above P1577):
//char frameorder[]={"bg"};
//no CEL

//Let's make up a new frame 'g'=0b1101001100
//char frameorder[]={"bg"};
//P1445

//Let's just start at 0 and work up to 255.  I think there's a start bit (data goes high), followed by 8 bits of data.
//'g'=0b1 00000 000 no CEL
//'g'=0b1 00000 001 no CEL
//'g'=0b1 00000 010 no CEL
//'g'=0b1 00000 011 no CEL
//'g'=0b1 00000 100 no CEL
//'g'=0b1 00000 101 no CEL
//'g'=0b1 00000 110 no CEL
//'g'=0b1 00000 111 no CEL
//'g'=0b1 00001 000 no CEL
//'g'=0b1 00001 001 no CEL
//'g'=0b1 00001 010 no CEL
//'g'=0b1 00001 011 no CEL
//'g'=0b1 00001 100 no CEL
//'g'=0b1 00001 101 no CEL
//'g'=0b1 00001 110 no CEL
//'g'=0b1 00001 111 no CEL
//'g'=0b1 00010 000 no CEL
//'g'=0b1 00010 001 no CEL
//'g'=0b1 00010 010 no CEL
//'g'=0b1 00010 011 no CEL
//'g'=0b1 00010 100 no CEL
//'g'=0b1 00010 101 no CEL
//'g'=0b1 00010 110 P1449
//'g'=0b1 00010 111 no CEL
//'g'=0b1 00011 000 no CEL
//'g'=0b1 00011 001 no CEL
//'g'=0b1 00011 010 no CEL
//'g'=0b1 00011 011 no CEL
//'g'=0b1 00011 100 no CEL
//'g'=0b1 00011 101 no CEL
//'g'=0b1 00011 110 P1647
//'g'=0b1 00011 111 no CEL
//'g'=0b1 00100 000 no CEL
//'g'=0b1 00100 001 no CEL
//'g'=0b1 00100 010 no CEL
//'g'=0b1 00100 011 no CEL
//'g'=0b1 00100 100 no CEL
//'g'=0b1 00100 101 no CEL
//'g'=0b1 00100 110 P1438
//'g'=0b1 00100 111 no CEL
//'g'=0b1 00101 000 no CEL
//'g'=0b1 00101 001 no CEL
//'g'=0b1 00101 010 no CEL
//'g'=0b1 00101 011 no CEL
//'g'=0b1 00101 100 no CEL
//'g'=0b1 00101 101 no CEL
//'g'=0b1 00101 110 no CEL
//'g'=0b1 00101 111 no CEL
//'g'=0b1 00110 000 no CEL
//'g'=0b1 00110 001 no CEL
//'g'=0b1 00110 010 no CEL
//'g'=0b1 00110 011 no CEL
//'g'=0b1 00110 100 no CEL
//'g'=0b1 00110 101 no CEL
//'g'=0b1 00110 110 P1584
//'g'=0b1 00110 111 no CEL
//'g'=0b1 00111 000 no CEL
//'g'=0b1 00111 001 no CEL
//'g'=0b1 00111 010 no CEL
//'g'=0b1 00111 011 no CEL
//'g'=0b1 00111 100 no CEL
//'g'=0b1 00111 101 no CEL
//'g'=0b1 00111 110 P1565
//'g'=0b1 00111 111 no CEL
//'g'=0b1 01000 000 no CEL
//'g'=0b1 01000 001 no CEL
//'g'=0b1 01000 010 no CEL
//'g'=0b1 01000 011 no CEL
//'g'=0b1 01000 100 no CEL
//'g'=0b1 01000 101 no CEL
//'g'=0b1 01000 110 P1635
//'g'=0b1 01000 111 no CEL
//'g'=0b1 01001 000 no CEL
//'g'=0b1 01001 001 no CEL
//'g'=0b1 01001 010 no CEL
//'g'=0b1 01001 011 no CEL
//'g'=0b1 01001 100 no CEL
//'g'=0b1 01001 101 no CEL
//'g'=0b1 01001 110 no CEL
//'g'=0b1 01001 111 no CEL
//'g'=0b1 01010 000 no CEL
//'g'=0b1 01010 001 no CEL
//'g'=0b1 01010 010 no CEL
//'g'=0b1 01010 011 no CEL
//'g'=0b1 01010 100 no CEL
//'g'=0b1 01010 101 no CEL
//'g'=0b1 01010 110 P1586
//'g'=0b1 01010 111 no CEL
//'g'=0b1 01011 000 no CEL
//'g'=0b1 01011 001 no CEL
//'g'=0b1 01011 010 no CEL
//'g'=0b1 01011 011 no CEL
//'g'=0b1 01011 100 no CEL
//'g'=0b1 01011 101 no CEL
//'g'=0b1 01011 110 P1580
//'g'=0b1 01011 111 no CEL
//'g'=0b1 01100 000 no CEL
//'g'=0b1 01100 001 no CEL
//'g'=0b1 01100 010 no CEL
//'g'=0b1 01100 011 no CEL
//'g'=0b1 01100 100 no CEL
//'g'=0b1 01100 101 no CEL
//'g'=0b1 01100 110 no CEL
//'g'=0b1 01100 111 no CEL
//'g'=0b1 01101 000 no CEL
//'g'=0b1 01101 001 no CEL
//'g'=0b1 01101 010 no CEL
//'g'=0b1 01101 011 no CEL
//'g'=0b1 01101 100 no CEL
//'g'=0b1 01101 101 no CEL
//'g'=0b1 01101 110 P1568
//'g'=0b1 01101 111 no CEL
//switched to only testing cases where last three bits '110'... I suspect '110' is an alert mask.
//'g'=0b1 01110 110 P1582
//'g'=0b1 01111 110 P1440
//'g'=0b1 10000 110 no CEL
//'g'=0b1 10001 110 no CEL
//'g'=0b1 10010 110 P1448
//'g'=0b1 10011 110 P1581
//'g'=0b1 10100 110 P1445
//'g'=0b1 10101 110 no CEL
//'g'=0b1 10110 110 P1583
//'g'=0b1 10111 110 P1572
//'g'=0b1 11000 110 P1439
//'g'=0b1 11001 110 P1573 (no CEL though)
//'g'=0b1 11010 110 P1585
//'g'=0b1 11011 110 P1576
//'g'=0b1 11100 110 P1577
//'g'=0b1 11101 110 P1648
//'g'=0b1 11110 110 P1649 (no CEL though)
//'g'=0b1 11111 110 no CEL

//so given the data and theory above, I should be able to set three P codes (arbitrarily picked the last 3: P1648/P1577/P1576)
//char frameorder[]={"bgbgbhbhbjbj"};
//Success.  The above three errors show up exactly as expected.  Unless there are more hidden codes elsewhere, we've got this cat skinned.

//Summary: 1 start bit (high), followed by 8 data bits.  IMA errors always end in '110'.  Thus, all IMA errors take form 0b1xxxxx110.
//21 'hard' IMA errors identified ('hard'=CEL illuminated)
//2 'soft' IMA errors identified ('soft'=CEL not lit).  There are probably more 'soft' IMA errors

//Leaving us with a known good IMA output:
char frameorder[]={"bc"};

void setup() {
pinMode(MOTFSApin,OUTPUT);  //clock
pinMode(MOTFSBpin,OUTPUT);  //data
Serial.begin(115200);
}

void loop() 
{
  for(int ii=0;ii<sizeof(frameorder);ii++)  //replace '10' w/ 'sizeof(frameorder)'
  { Serial.println("");
    bitbang_MOTFSB_frame(frameorder[ii]);
  }
}

void bitbang_MOTFSB_frame(char nn)
{  
  if (nn=='g')  //note: 'g' is a variable bitstream with no set pattern.
  {
    bangbit(1); //start bit (always high, defines frame)
    
    bangbit(1); //data bit 1 (MSB)
    bangbit(1); //data bit 2
    bangbit(1); //data bit 3
    bangbit(0); //data bit 4
    bangbit(1); //data bit 5
    
    bangbit(1); //data bit 6
    bangbit(1); //data bit 7
    bangbit(0); //data bit 8 (LSB)
    bangbit(0); //always low(?)
    Serial.print("G");
  }
  else if(nn=='a')
  {
    bangbit(1);
    bangbit(1);
    bangbit(1);
    bangbit(1);
    bangbit(1);
    bangbit(1);
    bangbit(1);
    bangbit(1);
    bangbit(1);
    bangbit(0);  
    Serial.print("A");
  }
  else if (nn=='b')
  { 
    bangbit(0);
    bangbit(0);
    bangbit(0);
    bangbit(0);
    bangbit(0);
    bangbit(0);
    bangbit(0);
    bangbit(0);
    bangbit(0);
    bangbit(0); 
    Serial.print("B");
  }
  else if (nn=='c')
  { 
    bangbit(1);
    bangbit(1);
    bangbit(0);
    bangbit(0);
    bangbit(1);
    bangbit(1);
    bangbit(0);
    bangbit(0);
    bangbit(0);
    bangbit(0); 
    Serial.print("C");
  }
  else if (nn=='d')
  {
    bangbit(1);
    bangbit(1);
    bangbit(1);
    bangbit(1);
    bangbit(0);
    bangbit(1);
    bangbit(1);
    bangbit(0);
    bangbit(0);
    bangbit(0); 
    Serial.print("D");
  }
  else if (nn=='e')
  {
    bangbit(1);
    bangbit(1);
    bangbit(1);
    bangbit(1);
    bangbit(0);
    bangbit(1);
    bangbit(1);
    bangbit(1);
    bangbit(0);
    bangbit(0); 
    Serial.print("E");
  }
  else if (nn=='f')
  {
    bangbit(1);
    bangbit(1);
    bangbit(0);
    bangbit(0);
    bangbit(1);
    bangbit(1);
    bangbit(1);
    bangbit(1);
    bangbit(0);
    bangbit(0); 
    Serial.print("F");
  }
    else if (nn=='h')
  {
    bangbit(1); //start bit (always high, defines frame)
    
    bangbit(1); //data bit 1 (MSB)
    bangbit(1); //data bit 2
    bangbit(1); //data bit 3
    bangbit(0); //data bit 4
    bangbit(0); //data bit 5
    
    bangbit(1); //data bit 6
    bangbit(1); //data bit 7
    bangbit(0); //data bit 8 (LSB)
    bangbit(0); //always low(?)
    Serial.print("H");
  }
  else if (nn=='j')
  {
    bangbit(1); //start bit (always high, defines frame)
    
    bangbit(1); //data bit 1 (MSB)
    bangbit(1); //data bit 2
    bangbit(0); //data bit 3
    bangbit(1); //data bit 4
    bangbit(1); //data bit 5
    
    bangbit(1); //data bit 6
    bangbit(1); //data bit 7
    bangbit(0); //data bit 8 (LSB)
    bangbit(0); //always low(?)
    Serial.print("J");
  }
}

void bangbit(bool jj)
{
    digitalWrite(MOTFSApin,LOW);  //clock low
    digitalWrite(MOTFSBpin,jj);  //set data
    delay(20);  //20 ms
    digitalWrite(MOTFSApin,HIGH);  //clock high
    delay(20);
}

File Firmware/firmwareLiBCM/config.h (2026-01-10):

//Copyright 2021-2024(c) John Sullivan
//github.com/doppelhub/Honda_Insight_LiBCM

//config.h - compile time configuration parameters

#ifndef config_h
    #define config_h
    #include "src/libcm.h"

    #define FW_VERSION "0.9.5n"
    #define BUILD_DATE "2025JUL07"

    //////////////////////////////////////////////////////////////////

    ///////////////////////////////////////
    //                                   //
    //  Hardware Specific Configuration  //
    //                                   //
    ///////////////////////////////////////

    //'choose' exactly one hardware option from each group below, which must match the actual installed hardware.
    //'choose' an option by removing both forward slashes ('//') at the beginning of that line.
    //all other options in each group MUST begin with two forward slashes (i.e. they are not chosen).
    //there are no default options because this firmware works with all LiBCM variants... you need to specify which hardware you have installed

    //choose your battery type:
        //#define BATTERY_TYPE_5AhG3 //if you're not sure, you probably have this battery
        //#define BATTERY_TYPE_47Ah  //aka FoMoCo //aka Samsung SDI modules

    //choose how many cells are in series:
        //#define STACK_IS_48S //All 5AhG3 Kits & 47Ah Kits with QTY4 modules
        //#define STACK_IS_60S //47Ah Kits with QTY5 modules

    //choose which grid charger is installed
        //#define GRIDCHARGER_IS_NOT_1500W //All 5AhG3 Kits & 'standard' 47Ah Kits
        //#define GRIDCHARGER_IS_1500W     //47Ah Kits with 'fast' 6.5A charger

    //choose ONE of the following
    //must match actual "current hack" hardware configuration:
        //#define SET_CURRENT_HACK_40 //actually +45.8% //most LiBCM users installed this hardware option
        //#define SET_CURRENT_HACK_20 //actually +25.0%
        //#define SET_CURRENT_HACK_00 //OEM configuration (no current hack installed inside MCM)

    //choose which display to use
    //using both displays simultaneously could cause timing issues (FYI: the Serial Monitor prints '*' each time the loop period is violated)
        #define LCD_4X20_CONNECTED  //display included with all LiBCM Kits
        //#define LIDISPLAY_CONNECTED //optional color touch screen display //JTS2doLater: mudder has not yet tested this code. Use at your own risk.

    //you don't need to change any settings below this line (but you can if you know what you're doing):
    //__________________________________________________________________________________________________

    //////////////////////////////////////////////////////////////////

    ////////////////////////
    //                    //
    //  Voltage Spoofing  //
    //                    //
    ////////////////////////

    //'choose' exactly one option from each group below.
    //the default values below should work in all cars.
    //modify these parameters if you want more power during heavy assist and/or regen.

    //48S ONLY: choose ONE of the following
    //60S MUST use 'VOLTAGE_SPOOFING_DISABLE':
        #define VOLTAGE_SPOOFING_DISABLE              //spoof maximum possible pack voltage at all times //closest to OEM behavior
        //#define VOLTAGE_SPOOFING_ASSIST_ONLY_VARIABLE //increase assist power by variably   spoofing pack voltage during assist
        //#define VOLTAGE_SPOOFING_ASSIST_ONLY_BINARY   //increase assist power by statically spoofing pack voltage during heavy assist
        //#define VOLTAGE_SPOOFING_ASSIST_AND_REGEN     //increase assist and regen power by variably spoofing pack voltage //DEPRECATED (regen too strong)
        //#define VOLTAGE_SPOOFING_LINEAR               //increase assist and regen power by requesting peak current level as per OEM (compatible with 100A fuse)

    //48S ignores this parameter (choose any value)
    //60S ONLY: to increase assist power, choose the lowest spoofed voltage that doesn't cause p-codes during heavy assist (e.g. P1440)
        //#define MIN_SPOOFED_VOLTAGE_60S 180 //voltage spoofing related p-codes won't occur in any car
        //#define MIN_SPOOFED_VOLTAGE_60S 175
        #define MIN_SPOOFED_VOLTAGE_60S 170 //recommended starting value //choose higher voltage if p-codes occur during heavy assist
        //#define MIN_SPOOFED_VOLTAGE_60S 165
        //#define MIN_SPOOFED_VOLTAGE_60S 160
        //#define MIN_SPOOFED_VOLTAGE_60S 155
        //#define MIN_SPOOFED_VOLTAGE_60S 150 //voltage spoofing related p-codes will occur in most cars during heavy assist

    //////////////////////////////////////////////////////////////////

    /////////////////////////
    //                     //
    //  Firmware Settings  //
    //                     //
    /////////////////////////

    //the default values below will work in any car.
    //you only need to modify these parameters if you don't like the default behavior.
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

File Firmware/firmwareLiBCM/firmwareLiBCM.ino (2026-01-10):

//Copyright 2021-2024(c) John Sullivan
//github.com/doppelhub/Honda_Insight_LiBCM
//Lithium battery BMS for G1 Honda Insight.  Replaces OEM BCM module.

#include "src/libcm.h"

void setup() 
{
    //getting here takes ~02 milliseconds after poweron reset
    //getting here takes ~16 milliseconds after IMA switch on
    gpio_begin();
    wdt_disable();
    LiControl_begin(); //SPI errors until initialized
    LTC68042configure_initialize();
    USB_begin();
    METSCI_begin();
    BATTSCI_begin();
    heater_begin();
    eeprom_begin();
    LiDisplay_begin();
    powerSave_init();

    if (gpio_keyStateNow() == GPIO_KEY_ON) { keyOn_coldBootTasks();          }
    else                                   { debugUSB_printWelcomeMessage(); }

    bringupTester_gridcharger(); 
    bringupTester_motherboard();

    wdt_enable(WDTO_2S); //set watchdog reset vector to 2 seconds
}

void loop()
{
    key_stateChangeHandler();
    time_handler();
    temperature_handler();
    SoC_handler();
    fan_handler();
    heater_handler();
    gridCharger_handler();
    buzzer_handler();
    lcdState_handler();
    LiDisplay_handler();
    batteryHistory_handler();
    cellBalance_handler();
    energy_handler();

    if (key_getSampledState() == KEYSTATE_ON)
    {
        if (eeprom_expirationStatus_get() != FIRMWARE_EXPIRED) { BATTSCI_sendFrames(); } //P1648 when firmware expired

        LTC68042cell_nextVoltages(); //round-robin handler measures QTY3 cell voltages per call
        METSCI_processLatestFrame();
        adc_updateBatteryCurrent();
        vPackSpoof_setVoltage();
        debugUSB_printLatestData();
        LiControl_handler();
    }
    else if (key_getSampledState() == KEYSTATE_OFF)
    {
        if (time_isItTimeToPerformKeyOffTasks() == YES)
        {
            LTC68042cell_acquireAllCellVoltages();
            SoC_updateUsingLatestOpenCircuitVoltage();
            powerSave_turnOffLiBCM_ifPackEmpty();
            debugUSB_printLatest_data_gridCharger();
        }
        else
        {
            powerSave_turnOffIfAllowed();
            powerSave_sleepIfAllowed();
        }
    }

    USB_userInterface_handler();
    wdt_reset(); //Feed watchdog
    LED_heartbeat();
    time_waitForLoopPeriod(); //wait here until next iteration
}

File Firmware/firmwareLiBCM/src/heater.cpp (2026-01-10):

//Copyright 2023-2023(c) John Sullivan
//github.com/doppelhub/Honda_Insight_LiBCM

//handles pack heater (if installed)

#include "libcm.h"

uint8_t heaterLocation = HEATER_NOT_CONNECTED;

//JTS2doLater: Add indicator to 4x20 when heater is off/on
//JTS2doLater: Turn all discharger resistors on when pack is heating.

/////////////////////////////////////////////////////////////////////////////////////////

uint8_t heater_isConnected(void) { return heaterLocation; }

/////////////////////////////////////////////////////////////////////////////////////////

bool isHeaterConnectedtoPin(int16_t pinToTest)
{
    uint8_t initialPinMode = gpio_getPinMode(pinToTest);
    bool isHeaterConnectedToThisPin = NO;

    pinMode(pinToTest,INPUT_PULLUP);

    if (digitalRead(pinToTest) == false)
    {
        isHeaterConnectedToThisPin = YES; //if connected, the isolated driver on the heater PCB will pull signal low
        digitalWrite(pinToTest,LOW); //turn heater off
        pinMode(pinToTest,INPUT); //switch pin to input (redundant, for safety)
    } 
    else { pinMode(pinToTest,initialPinMode); } //heater not connected to this pin

    return isHeaterConnectedToThisPin;
}

/////////////////////////////////////////////////////////////////////////////////////////

//determine if heater installed, and if so, which GPIO pin it's connected to
void heater_begin(void)
{
    if (isHeaterConnectedtoPin(PIN_GPIO1) == true) { heaterLocation = HEATER_CONNECTED_DAUGHTERBOARD;   }
    if (isHeaterConnectedtoPin(PIN_GPIO3) == true) { heaterLocation = HEATER_CONNECTED_DIRECT_TO_LIBCM; }
}

/////////////////////////////////////////////////////////////////////////////////////////

bool hasEnoughTimePassedToChangeState(void)
{
    static uint32_t timestamp_latestChange_ms = 0;

    bool hasEnoughTimePassed = NO;

    if ((millis() - timestamp_latestChange_ms) > HEATER_STATE_CHANGE_HYSTERESIS_ms)
    {
        hasEnoughTimePassed = YES;
        timestamp_latestChange_ms = millis();
    }
    
    return hasEnoughTimePassed;
}

/////////////////////////////////////////////////////////////////////////////////////////

bool heater_isPackTooHot(void)
{
    if ((temperature_battery_getLatest() > FORCE_HEATER_OFF_ABOVE_TEMP_C) ||
        (temperature_battery_getLatest() == TEMPERATURE_SENSOR_FAULT_LO)   ) //assume pack too hot if temp sensors disconnected
         { return YES; }
    else { return NO;  }
}

/////////////////////////////////////////////////////////////////////////////////////////

void heater_handler(void)
{
    if ((powerSave_isThermalManagementAllowed() == NO) || //not enough energy to heat pack
        (heater_isConnected() == HEATER_NOT_CONNECTED) || //heater not installed         
        (heater_isPackTooHot() == YES)                  ) //pack is too hot
    { gpio_turnPackHeater_off(); } //heater not allowed

    else //heater is allowed
    {
        if (hasEnoughTimePassedToChangeState() == YES)
        {
            if (temperature_battery_getLatest() < temperature_heatBatteryBelow_C()) { gpio_turnPackHeater_on();  } //pack is     cold
            else                                                                    { gpio_turnPackHeater_off(); } //pack is not cold
        }
    }
}

/////////////////////////////////////////////////////////////////////////////////////////

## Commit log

2021-03-10 Initial Commit
    Not much here yet...
    [Cable Primitive.dwg, Cable Primitive.ipt, LiBCM End Plate - RevA.dwg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]
2021-05-16 RevA PCB Commit
    A lot has changed.
    [BCM Pinouts 2020MAR03 Mega.ods, G3Lithium QTY Purchased.ods, LT1797 Gain Calculation.ods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]
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2021-05-18 Limited Variable Scope in switch statement
    Fixed odd issue where case 9 wouldn't work.
2021-05-20 Prototyped voltage-based grid disable
    [LiBCM BOM - RevA.ods]
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2021-06-02 Removed .DS_Store Files For Good
    [LiBCM BOM - RevB.ods]
2021-06-03 Outlined Tasks & MVP. BCM sensor calibration data.
    [Measured OEM Current Sensor Behavior with Modified Output.ods]
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2021-06-04 1st Attempt at generating BATTSCI
    Didn't see any reason to build the frames into an array... just placing each element into the serial send buffer as soon as it's created. Should be faster, unless Serial.write() is inefficient.
    [BATTSCI.ino, METSCI.ino, MVP.ino]
2021-06-04 Added KEYON state change logic
    Also fixed BATTSCI init bug (wrong port number).
    [BATTSCI.ino, MVP.ino]
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2021-06-07 Adding in LTC68042 SPI code
    [LiBCM BOM - RevB.ods]
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2021-06-08 Negated BATTSCI current value
    Also changed how BATTSCI sends frames (it now ping-pongs between the two). Added new CAR about how MCM is suddenly drooping Connector E voltage... I guess it behaves differently when actually installed in the car (and all the signals are present... so no P-codes). We can certainly fix this issue in firmware (e.g. by spoofing voltage down to match)... but a better solution is to add more capacitance and/or lower the resistance to the spoofing voltage divider.
    [BATTSCI.ino]
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2021-06-12 Final BOM prep prior to RevB Assembly
    [G3Lithium QTY Purchased.ods, LiBCM BOM - RevB.ods, LiBCM End Plate - RevA.dwg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]
2021-06-13 Voltage spoofing tests and related CARs
    [voltage spoofing test.ods]
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2021-06-30 RevB V&V
    Lots of changes... probably waited too long to push.
    [LiBCM BOM - RevB.ods, LiBCM-centroids-PNP 2021JUN17.csv, LiBCM-centroids-PNP 2021JUN18.csv]
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2021-07-03 Update BOM, minor firmware changes.
    [LiBCM BOM - RevB.ods]
2021-07-12 Adding floating BATTSCI pin fix to grid charger code.
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2021-07-22 Fan turns on when key on, isoSPI error counting
    Added error counting info to 4x20 display to count isoSPI CRC failures
    [MVP.ino]
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2021-07-27 Added LED4 heartbeat
    Also added test code for Peter's hardware issue.
    [BATTSCI.ino, METSCI.ino]
2021-07-29 Added LTC6804 per-register error counted
    When an error occurs, serial monitor outputs array of tallied errors per Cell Voltage Register.
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2021-08-03 LED3 now turns on if LiBCM resets while key is on
    If LED3 is on, that indicates LiBCM reset (and recovered) while driving.
    [MVP.ino]
2021-08-06 Inline 5.5k to 6.0k resistor now required on VPIN to MCM
    LiBCM now reports 94% of actual pack voltage to MCM. This is to prevent P1576 during heavy regen.
    [LiBCM BOM - RevB.ods]
2021-08-13 Added different I2C Library
    Wasn't able to fix I2C data hang, but decided to keep both I2C drivers, since the new one is better. However, for now, I'm still using the old driver (using #ifdef to select which driver to call).
    The only difference between 0.0.11 & 0.0.13 is that I clear the 4x20 display when the key is off (previously I just turned the backlight off).
    [MVP.ino]
2021-08-13 0.0.12NM Fixed display issues.
2021-08-17 Removed all .ino files, except MVP.ino
    Goal is to remove Arduino SDK entirely, but since we're still using many internal Arduino-specific functions this didn't work out. I could get the code to build and upload (i.e. with main.c instead of MVP.ino)... however, many core functionalities wouldn't work. Probably a missing header file, but decided to bail on this for now. Will revisit later.
    [MVP.ino, battsci.cpp, config.h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]
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2021-08-18 Setup to measure MCM'E' Voltage Error
    Using external power supply, ignoring LTC6804 voltages... spoofing Vpack via manual user entry
    [MVP.ino]
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2021-08-20 Architecture Rework
    Added adc.c, vPack spoofing, and lots of other things.
    [MVP.ino, adc.cpp, adc.h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]
2021-08-21 Adding timing measurements
    Also started pulling lcd2 calls into separate file.
    [12S Module.0003.ipt, 12S Module.ipt, 18S Module.0003.ipt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]
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2021-08-22 Fixed Natalya's P-code when I2C data line held low
    [config.h, lcd_I2C.cpp]
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2021-08-25 Added ECM Spoofing Test Fixtures
    [lcd_I2C.cpp, lcd_I2C.h]
2021-08-27 Making SuperLoop Faster
    BATTSCI 100 ms delay is no longer blocking.
    LED behavior now config.h configurable (debug versus production).
    LED functions moved to debugLED.c
    Per-Loop USB Serial data now lives in debugUSB.c
    USB Serial data only sent every 500 ms
    LEDs now blink at 5 Hz, no matter how fast code is running.
    [MVP.ino, adc.cpp, battsci.cpp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]
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2021-08-28 Fixed PEC mismatch on returned LTC data stream
    [lcd_I2C.cpp]
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2021-09-01 New VPIN_spoof equation
    Added 2005+ BATTSCI fix (72% SoC)
    [battsci.cpp]
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2021-09-02 Testing ESR offset calculation
    Reduced repository size (compressed/deleted files)
    [12S Module.0003.ipt, 18S Module.0003.ipt, Cell.0002.ipt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]
2021-09-02 SoC now linked to cell voltage
    Previously using spoofed pack voltage
    [vCellWithESR_counts data.ods]
2021-09-03 determined vSpoof equation
    It ain't pretty
    [spoofingVoltage Calculations.ods]
2021-09-04 Adder cell undervoltage test
    Disables assist if any cell voltage is too low.
    [battsci.cpp]
2021-09-04 Added regen/assist disable flags
    If cell voltage is too high/low, regen/assist are disabled.
    [battsci.cpp, config.h, gridCharger.cpp]
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2021-09-19 Schematic complete
    Still considering adding a few items, but probably done.
    [LiBCM BOM - RevC.ods, LiBCM-2021-03-18-16-48-35.sch, LiBCM-2021-03-18-18-33-24.sch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]
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2021-10-13 Thinner Safety Cover
    Also updated Fan cap to 2 uF, and generated centroids.
    [Assembly - Before Cover.iam, Fan.ipt, IMA Battery Case Primitive.ipt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]
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2021-10-30 P&P Centroids Updated
    Changes made with building QTY20 PCBs.
    [LiBCM2021OCT29.csv]
2021-10-30 Updated BOM (opamp stability)
    [LiBCM2021OCT29.csv]
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2021-11-10 Loosened 0A ADC limits
    Going to add a key-off calibration
    [config.h]
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2021-11-12 Added Intermediate SoC uC Buffer
    Adds more resolution to the state of charge integrator. Also removed a multiply and QTY19 shifts (replaced with addition).
    [adc.cpp, adc.h, config.h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]
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2021-11-18 Updated 4x20 Layout, SoC changes
    Added:
    -BMS cable drawing,
    -SoC updates every 30 minutes when the key is off.
    -LiBCM now turns itself off if the key is off and any cell drops below 7% SoC (to prevent severe battery discharge),
    -LiBCM now displays uptime each time the SoC updates (and the key is off).
    -4x20 display now has SoC, hi/lo temps, and current,
    -removed error count from 4x20 display,
    -added 4x20 and buzzer alert if grid charger plugged in while key on,
    -several new fcns to get/set SoC,
    -added LUT to estimate SoC based on open-circuit voltage,
    -bumped version to 0.4.0, because it felt good.
    [cell charge discharge data.ods]
2021-11-21 Temperature and LCD updates
    Other changes:
    -Removed old I2C LCD libraries
    -MCM'E' goes high impedance when keyOFF
    [thermistor temperature math.ods]
2021-11-21 Revert BATTSCI temp
    Need to figure out what formatting MCM is expecting.
    [battsci.cpp]
2021-11-22 Fixed errant buzzer while grid charging
    If any single cell sample voltage was too high, the buzzer was set (to warn the user). However, when the cell voltage dropped back down, the buzzer wasn't cleared (and so never turned off).
    Also pushed all Serial text to flash memory (instead of RAM).
    Cell19 voltage adjustment now enabled by default.
    [config.h, debugUSB.cpp, gridCharger.cpp]
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2021-12-13 Fixed temp sensor enable issue
    Temp sensors wouldn't always turn on.
    [config.h, gpio.cpp]
2022-01-08 Comments with bugs to fix
    [LiBCM BOM - RevC.ods]
2022-01-16 LiBCM no longer bricks, but still set P1648 after firmware expires
    Allow LiBCM to continue monitoring battery voltage and temperature.
    [eepromAccess.cpp, eepromAccess.h]
2022-01-17 battsci redesign
    Cleaned up battsci
    [LiBCM BOM - RevC.ods, Remap SoC.ods]
2022-01-17 Fixed SoC_percent double-bounding calculation bug
    This should make LiBCM behave better during heavy regen. Old code accidentally multiplied "pack full" variable by 85% twice... which made SoC percentage calculations incorrect (e.g. if SoC_actual is 85%, then LiBCM's estimator would calculate SoC_prediction at 72% (0.85*0.85).
    [adc.cpp, config.h]
2022-01-18 Replaced variable calls inside SoC.cpp with respective functions
    [debugUSB.cpp]
2022-01-21 Prevent CEL during heavy assist when SoC is low
    [battsci.cpp, config.h]
2022-01-24 Fixed 7% SoC at first key on issue
    [battsci.cpp, config.h]
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2022-01-29 Disabled keyON SoC Display
    When LiBCM cold boots, keyON timing is very tight. If we send SoC text during keyON, that could cause a check engine light (if the serial buffer is full we'll hang until it empties).
    [battsci.cpp]
2022-02-01 Fixed max regen voltage
    [config.h]
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2022-02-02 Moved BATTSCI Assist/Regen Flag Byte
    Old FW sent flags on 0xAA@B06 (incorrect). New FW sends flags on 0xAA@B05 (which is what it was back in December, before I 'fixed' it).
    [LiBCM BOM - RevC.ods]
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2022-03-10 Separated grid charging from balancing
    New Features in LiBCM v0.7.0:
    -default current hack value is now +40%.
    -Removed RevB HW support (all Open Beta customers have RevC HW).
    -Can now disable assist and/or regen (as requested by Balto). See config.h>>DISABLE_ASSIST & DISABLE_REGEN.
    -Cell balancing now runs independently from grid charging.
    -Cells now balance to 0.5 mV (previously 1.0 mV).
    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
    [LiBCM BOM - RevC.ods]
2022-03-14 Simplified LTC6804 WRCFG command
    Also fixed grid charger status display on 4x20 LCD.
    [LTC68042configure.cpp, config.h, key.cpp]
2022-03-17 keyOFF power consumption reduced (similar to v0.6.8)
    Changes from v0.7.0:
    -Even if SoC is low, LiBCM will not turn off for at least ten minutes after the key is turned off (see config.h>KEYOFF_TURNOFF_LIBCM_DELAY_MINUTES)
    -KeyOFF power consumption nearly identical to v0.6.8 (and MUCH less than v0.7.0)
    -Added LTC6804 discharge timer feature, which greatly reduces power consumption (see LTC68042configure_setBalanceResistors)
    -Restructured LTC6804 watchdog timer architecture, which should fix intermittent keyOFF cell voltage oddities (e.g. 6.5535 volts). A single function ("LTC68042configure_wakeup") replaces both previous functions. Note: If the grid charger is plugged in immediately afte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
    [LTC68042configure.cpp, LTC68042configure.h, LTC68042gpio.cpp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]
2022-03-28 Added Watchdog
    LiBCM now resets if watchdog not fed for two seconds.
    [MVP.ino, config.h]
2022-04-08 Added runtime serial configuration architecture
    LiBCM now supports text-based user input, which allows users to runtime-configure LiBCM, which stores persistent values in EEPROM. Runtime testcode can now also be run (using $TEST_). This should improve debugging experience. Also put a bandaid on background regen issue when Calpod enabled (full fix to follow later). Also, when the key is first turned off, LiBCM now wait ten minutes before enabling cell balancing (to allow cell voltages to settle).
    [LiBCM BOM - RevC.ods]
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2022-04-12 BATTSCI packets now sent every 33 ms (previously 100 ms)
    [Day1Analysis.ods, Day2Analysis.ods, LiBCM BOM - RevC.ods]
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2022-05-07 Finished RevD PCB (except for possible HVAC switch change)
    [LiBCM BOM - RevD.ods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]
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2022-05-26 Prevent cell balancing if battery modules get too hot
    Eventually the temperature sensor should actually measure input air temperature (not module temperature). Good enough for now; if the cabin air is too hot, then LiBCM will run the fans and cell balance until the modules themselves heat up too much.
    [LiBCM BOM - RevD.ods]
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2022-07-23 Added runtime Vpack spoofing. Fixed MCM'e' PWM frequency
    [MCMe PWM Frequency.ods]
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2022-07-24 Added Long Term Cell Tester Program and test data
    [Part Dimensions.ods]
2022-08-02 Final data for Long term cell test #1
    [*summary.ods]
2022-08-05 Note to add false keyON test to logic
    This prevents over-discharging IMA battery if 12V_IMA remains 'on' for more than an hour without the engine running.
    [key.cpp]
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2022-08-06 Increased cell balancing Vdelta to 2.2 mV
    LTC6804 total measurement uncertainty is 2.2 mV... previous Vdelta was less than this value, hence the QTY5 LTC6804 ICs sometimes continuously attempted to balance cells below what they could accurately resolve... so basically cell balancing never stopped until SoC dropped below CELL_BALANCE_MIN_SoC.
    [LTC68042configure.cpp, LTC68042configure.h, config.h]
2022-08-06 Moved Long Term Cell Testing Results
    Find them here:
    https://github.com/doppelhub/Long-Term-Lithium-Cell-Tests
    [*summary.ods]
2022-08-07 New Fan Controller / Derived OEM Temp Constants
    Rewrote LiBCM's fan controller (in new fan.c file). Each subsystem (grid charger, cell balancer, etc) can now independently request fan speeds; highest fan speed (for each fan) wins.
    Also empirically derived (unknown) OEM temperature sensor constants, so we can accurately measure temperatures from the GRN/WHT/BLU/YEL OEM temp sensors.
    [OEM thermistor scaling.ods]
2022-08-11 LiDisplay - Fix Grid Charge Page
    [config.h, gpio.cpp, gpio.h]
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2022-08-23 moved fan logic (fan.c), added OEM temp sensors
    [LiBCM BOM - RevD.ods]
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2022-08-23 Added periodic forced fan state update
    Lazily handles keyOFF event, where fan enable conditions get more strict (to save battery).
    [LiBCM BOM - RevD.ods]
2022-08-25 Added 47Ah FoMoCo SoC<->VoC LUT
    LiBCM now supports two lithium chemistries!
    [Decimated.ods, LiBCM BOM - RevD.ods]
2022-08-25 Updated VoC->SoC LUT
    Old LUT used fast discharge data (around 1C). New LUT discharged cell much slower (around 1/16C). This should make keyOFF SoC calibration more accurate.
    [Decimated.ods]
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2022-09-07 Fixed MCM-related VPIN underflow issue
    [config.h]
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2022-10-15 Fixed 32b millis() overflow. Started $DISP=DBG
    [47 Ah FoMoCo Aluminum Tray.0002.dwg, Label.ods, LiBCM BOM - RevD.ods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]
2022-11-22 new status.cpp, fixed user serial bug, 5AhG3 Heater PCBs
    [5AhG3-12S-B_Cu.gbl, 5AhG3-12S-B_Mask.gbs, 5AhG3-12S-B_Paste.gbp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]
2022-11-28 Prevent 60S P1440 During heavy assist in 3rd/4th/5th gear
    MCM gets upset when output current is too high (due to spoofed voltage). Probably a better way to fix this.
    [config.h]
2022-11-29 '$TestT' displays all temp sensors; 18S P&P file
    [18S-2022NOV28.csv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]
2022-12-01 PCB File Structure changed
    Now that LiBCM has multiple PCBs, added a new directory for "motherboard" and "daughterboard"
    [0-KiCAD Output (formatted).csv, A-LiBCM2022JUN13.csv, Assembly Time.ods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]
2022-12-08 Daughterboard RevA & 5AhG3 Heater RevB 5AhG3 PCBs
    [0 KiCAD output.csv, 02 Final Assembly (Tray Mated).iam, 18S-2022NOV28.csv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]
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2022-12-08 Flipped LED
    [12S-2022DEC07.csv]
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2022-12-31 Rewrote VOLTAGE_SPOOFING_ASSIST_ONLY_VARIABLE
    This is now the default (and recommended) voltage spoofing mode.
    [Cell Lifetime Comparison.ods, Decimated.ods, LiBCM BOM - RevD.ods]
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2023-01-29 Bug fix: Balancing allowed when grid charger plugged in
    [gridCharger.cpp, key.cpp]
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2023-02-01 Rewrote lcdState machine
    Fixed conservative heater logic
    [MVP.ino, config.h, debugUSB.cpp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]
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2023-04-10 Added a buzzer_handler() to service requests from multiple subsystems
    [MVP.ino]
2023-04-10 Consolidated gpio_turnBuzzer_* calls from lcdTransmit.cpp and gridCharger into isChargingAllowed(); Cleaned up and refactored reportChargerState() and powered_handler(); Fixed bug in reportChargerSta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
    [gridCharger.cpp, lcdTransmit.cpp]
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2023-06-09 Swapped temp sensors
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2023-06-13 Documented HW Issues
    [photovoltaic LED current consumption.ods]
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2023-07-13 Fixed SPI Flash_CS conflict
    [config.h, gpio.cpp]
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2023-08-28 isoSPI faults, gridCharger, amps->deciAmps,
    Vcell now set to 0 volts on isoSPI error, 4x20 power & current sign flipped (now '-' during assist), increased current sensor resolution from amps to deciamps, restructured gridCharger.c,
    [OEM Current Sensor.ods, Vpin Offset Calculation.ods]
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2023-08-31 config.h guardrails
    Also fixed LTC6804 error when calculating PEC on AUX registers.
    [LTC68042configure.cpp, LTC68042configure.h, LTC68042gpio.cpp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]
2023-09-01 formatting to prevent warnings
    No actual code changes.
    [LTC68042configure.cpp, cpu_map.h]
2023-09-02 Guardrail to prevent 60S 5AhG3
    [LTC68042configure.h]
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2023-09-23 disable watchdog during EEPROM reset
    [eepromAccess.cpp]
2023-09-23 Fixed double SoC integrator issue
    [batteryHistory.h, config.h, gridCharger.cpp]
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2023-09-24 added watchdog reset to eeprom erase
    [batteryHistory.cpp, config.h, eepromAccess.cpp]
2023-09-25 progress bar to eeprom reset
    [config.h, eepromAccess.cpp]
2023-09-27 Fix Avg cell vltg display on grid chrg page.
    [config.h]
2023-09-28 Fixed date, removed balancing note as it would only work if USB was plugged into a computer.
    [config.h, debugUSB.cpp]
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2023-11-05 Simplified Motherboard Tester
    No longer using thermal imager to verify LTC6804 discharge circuitry.
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2023-12-17 Moved files to /src/ folder
    There are no code changes except for firmware version bump (to 0.9.3b)
    [Analysis.ods, OEM thermistor scaling.ods, Vpin Offset Calculation.ods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]
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2024-03-05 LCD 'EFGH' Flags; simplified buzzer,
    [LTC68042configure.cpp, adc.cpp, config.h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]
2024-03-25 Constant Current Voltage Spoofing (VOLTAGE_SPOOFING_LINEAR) (#49)
    * Update vPackSpoof.cpp
    // adjusts spoof voltage across entire range so that current is 50A continuous, 83A peak
    // 48S yields from +19% power
    // 60S yields from +28% power
    // max spoofing is within 67% of Vpack
    // this is compatible with standard 100A OEM fuse.
    * Update vPackSpoof.cpp
    VOLTAGE_SPOOFING_LINEAR
    spoofedPackVoltage = actualPackVoltage * 0.4 + 72
    * Update config.h
    //#define VOLTAGE_SPOOFING_LINEAR
    * Update vPackSpoof.cpp
    * Update vPackSpoof.cpp
    correction to input voltage variable
    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
    [config.h]
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2024-05-02 Updates to LiDisplay (#48)
    * Version
    * Handle key and gc state changes inside LiDisplay.cpp instead of other files.
    * LIDISPLAY_SPLASH_PAGE_MS now in config.h
    * Updated handling of changes to power state
    * Fan speed button operation
    * remove comments
    * Fix merge conflicts
    * removed unintentional whitespace changes to two files
    * Remove user fan request when GC or key unplugged/off
    * deleted coments, added some preparations for cell voltage display while driving
    * Fixed bugs on GC page, added Balancing info to GC page, fixed ccell delta on driving page.
    * Switch to use new cellBalance_areCellsBalancing() function.
    [config.h, eepromAccess.h, gridCharger.cpp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]
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2024-07-24 Test Claim to fix frozen OEM SoC Gauge
    [adc.cpp, battsci.cpp]
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2024-10-21 Update BOM; fix bringupTester isoSPI issue
    [LiBCM BOM - RevD.ods]
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2024-11-27 Wh to 4x20, 48S||60S debug, buffer overflow fix
    [0-KiCAD Output (formatted).csv, A-LiBCM2022JUN13.csv, B-LiBCM2022JUN23.csv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]
2024-12-21 Revert to previous BATTSCI SoC
    [LiBCM BOM - RevD.ods]
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2025-02-27 First cut at re-mapping 5AhG3 thermistors to FoMoCo battery type.
    This aligns firmware thermistor use with the hardware. For the FoMoCo
    case, this is the thermistor use:
    5AhG3 FoMoCo
    OEM GRN: IMA Intake Top rear battery module
    OEM YEL: IMA Exhaust Top middle battery module
    OEM WHT: Ambient IMA Intake
    With the change, the OEM GRN and YEL thermistors now participate in
    temperature_measureBattery(), and no longer in temperature_measureOEM().
    Additionally, in the FoMoCo case, there are no explicit Exhaust and
    Ambient thermistors, so references to these are removved.
    [cpu_map.h, debugUSB.cpp, gridCharger.cpp]
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2025-06-18 Replaced 'FoMoCo' with '47Ah'
    Lithium modules are now referred to as '47Ah'.
    [config.h, cpu_map.h, debugUSB.cpp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]
2025-06-22 Rewrote processAllCellVoltages()
    Old function was messy due to 5AhG3cell#19 HW hack.
    Fixed trivial bug: Vpack didn't include actual cell#19 voltage.
    Added new functions:
    LTC68042result_hiCellNum_get() LTC68042result_loCellNum_get()
    [config.h]
2025-06-22 Revert to production values
    [config.h, eepromAccess.cpp]
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

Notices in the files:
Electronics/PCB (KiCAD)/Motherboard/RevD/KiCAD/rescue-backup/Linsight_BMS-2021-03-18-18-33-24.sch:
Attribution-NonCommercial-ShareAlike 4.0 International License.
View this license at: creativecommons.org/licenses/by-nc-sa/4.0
